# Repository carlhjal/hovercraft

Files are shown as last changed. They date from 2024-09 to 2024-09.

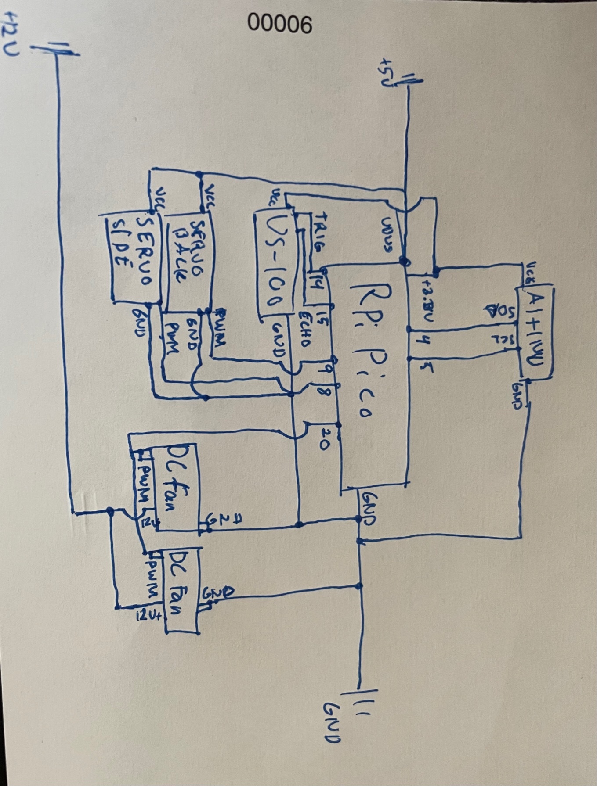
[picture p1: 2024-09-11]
diagram.jpg

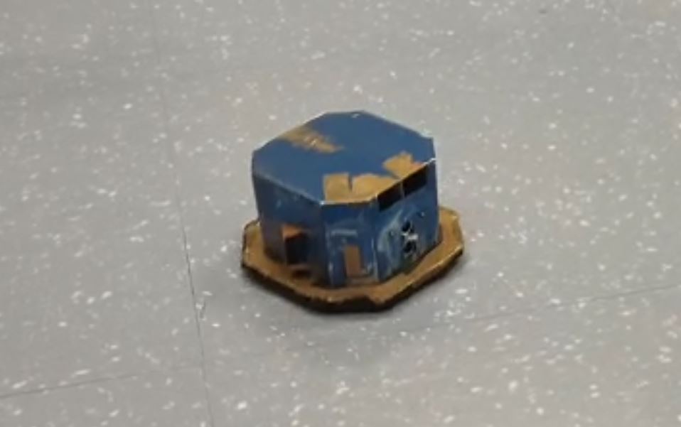
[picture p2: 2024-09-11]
image.JPG

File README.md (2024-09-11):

# Hovercraft

This is a Raspberry Pi Pico based project: a hovercraft capable of moving, steering and obstacle avoidance by use of an ultrasonic sensor and opening/closing shutters connected to its pressurized interior.

All the 3D printed parts from this project are available in the models folder.

PlatformIO is needed to build project "Robot Control Program".

A detailed/exploded view of the complete assembly is in the works..

Made as part of the Robotics Engineering Project course at the University of Tartu.

## Bill of materials
- x1 Raspberry Pi Pico
- x1 Breadboard
- x2 Turnigy TG9 Servo
- x1 US-100 ultrasonic sensor
- x2 GFB0412EHS-DF00 DC Fan
- x1 YB1203000-USB Battery (12V and 5V power supply)
- x1 AltIMU-10 v5
- x2 3D printed rail parts - "rail_lower_servo_fitting.STL"
- x2 3D printed shutters with racks - "lower_rack.STL"
- x1 3D printed US-100 fitting - "us-100-fitting.STL"
- x1 3D printed opening to fan duct - "intake_duct_smaller_fans.STL"
- x2 3D printed gear - "gear_final.STL"
- x1 3D printed base extender - "extension_plate.STL"
- x1 bottom skirt from extra durable trashbag
- x15 Male-to-male jumper cables
- x8 Male-to-female jumper cables
- x4 10mm M3 bolts with reduced head size
- x2 10mm M3 bolts
- x6 M3 nuts
- x1 12v Breakout cable
- x1 5v USB breakout cable
- Brown packing tape for airleak sealing and securing parts
- x1 cut cardboard duct for directing airflow from side outlet
- x1 cut cardboard flap for offsetting steering bias
- x1 cut cardboard for securing IMU on bottom plate

Any .STL files are available under models/stl_files

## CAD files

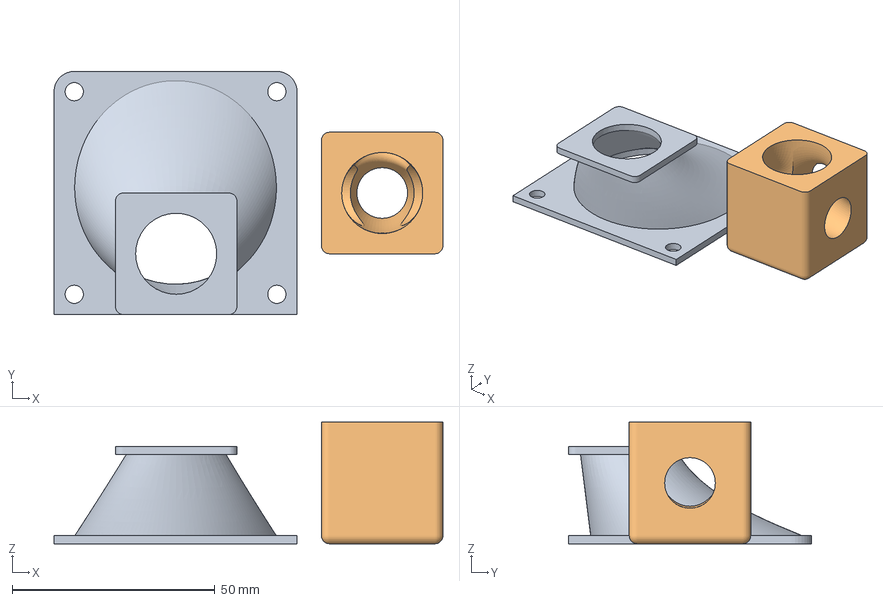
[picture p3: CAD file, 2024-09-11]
models/stl_files/air-divider^robotassembly.3mf
96.0 x 60.0 x 30.0 mm
duct-post-fan^robotassembly.STL
air-divider^robotassembly.STL

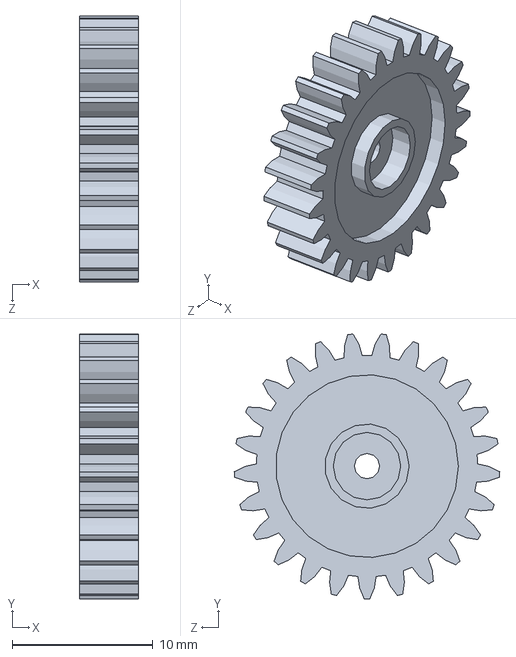
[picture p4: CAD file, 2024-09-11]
models/gear_final_asm.SLDPRT
4.20 x 18.8 x 18.9 mm

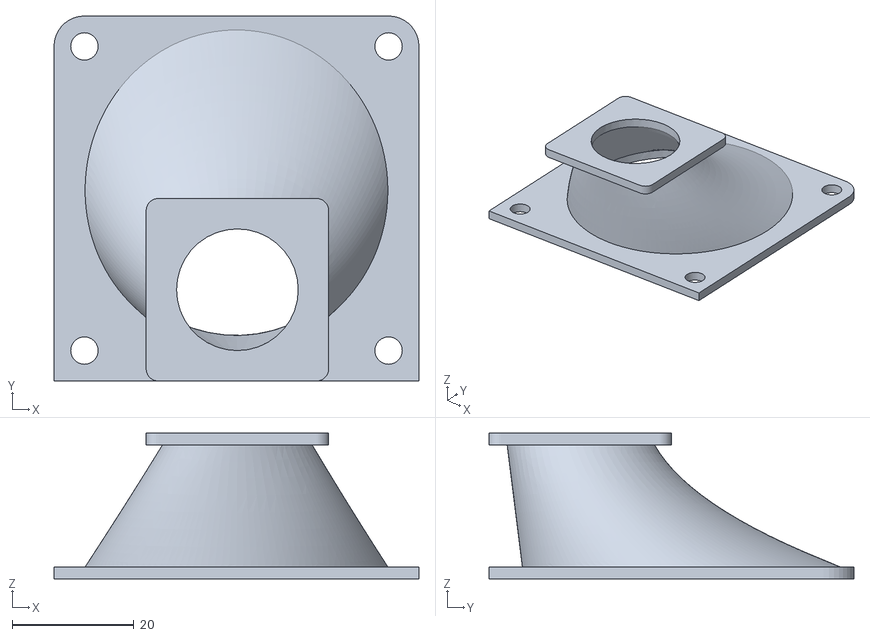
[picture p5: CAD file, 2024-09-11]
models/stl_files/duct-post-fan^robotassembly.STL
60.0 x 60.0 x 24.0

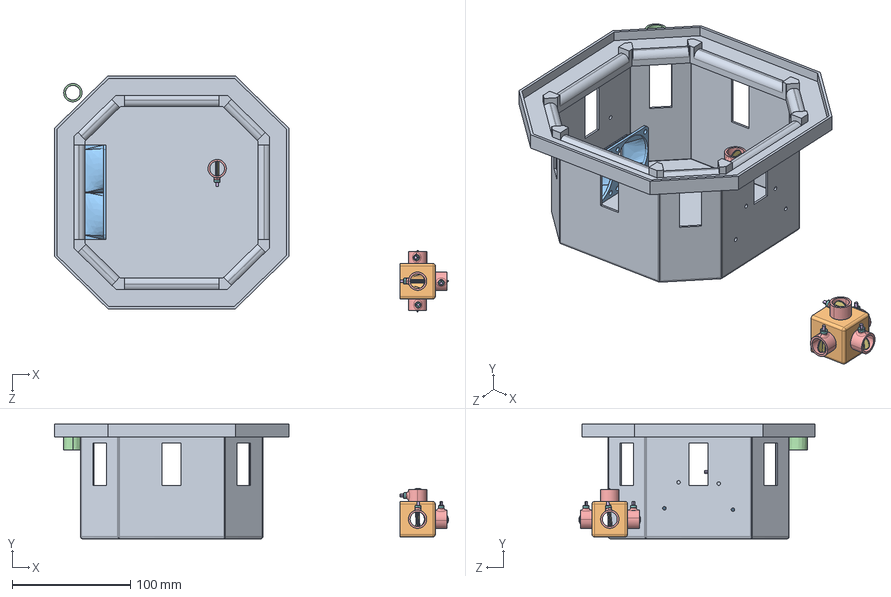
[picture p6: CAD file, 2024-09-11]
models/robotassembly.STEP
333.3 x 97.0 x 199.8 mm
air-divider^robotassembly
intake_duct_smaller_fans
tube_fitting
Butterfly_valve_tube x 5
shaft^Butterfly_valve x 5
plate^Butterfly_valve x 5
cap^Butterfly_valve x 5
extension_plate

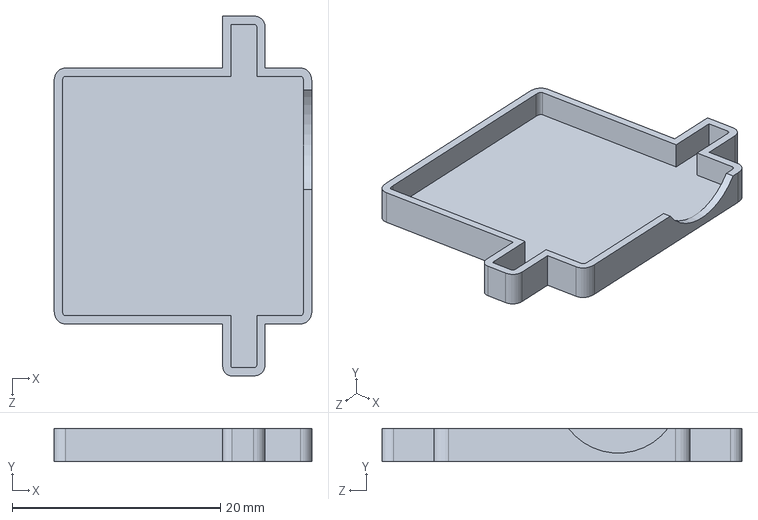
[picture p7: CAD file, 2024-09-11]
models/fitting_for_serv.SLDPRT
24.8 x 3.20 x 34.6 mm

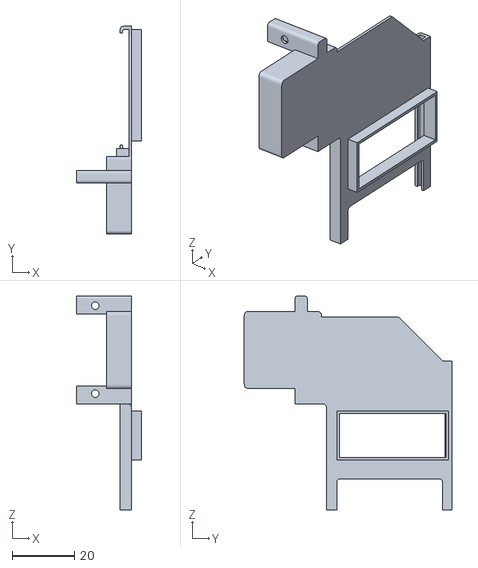
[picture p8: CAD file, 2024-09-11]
models/stl_files/rail_lower_servo_fitting.STL
20.8 x 66.5 x 68.6

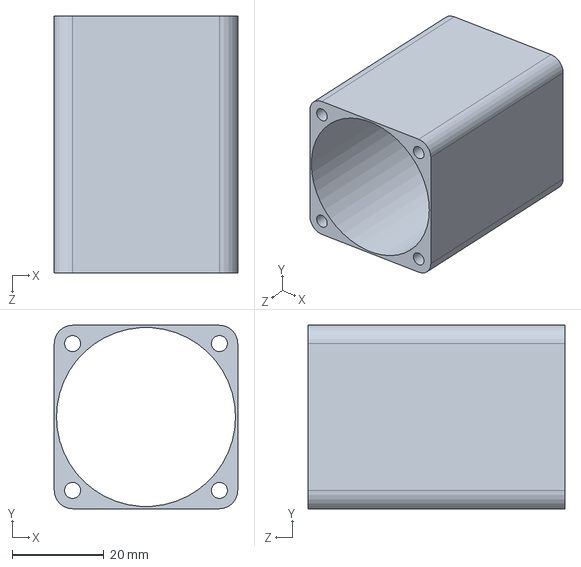
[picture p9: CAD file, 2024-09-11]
models/smaller_fan_rough.SLDPRT
40.0 x 40.0 x 56.0 mm

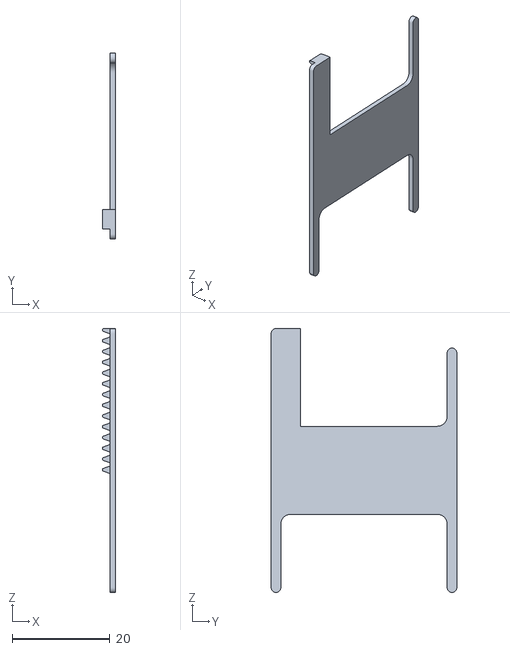
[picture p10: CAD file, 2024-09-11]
models/stl_files/lower_rack.STL
2.70 x 38.0 x 54.0

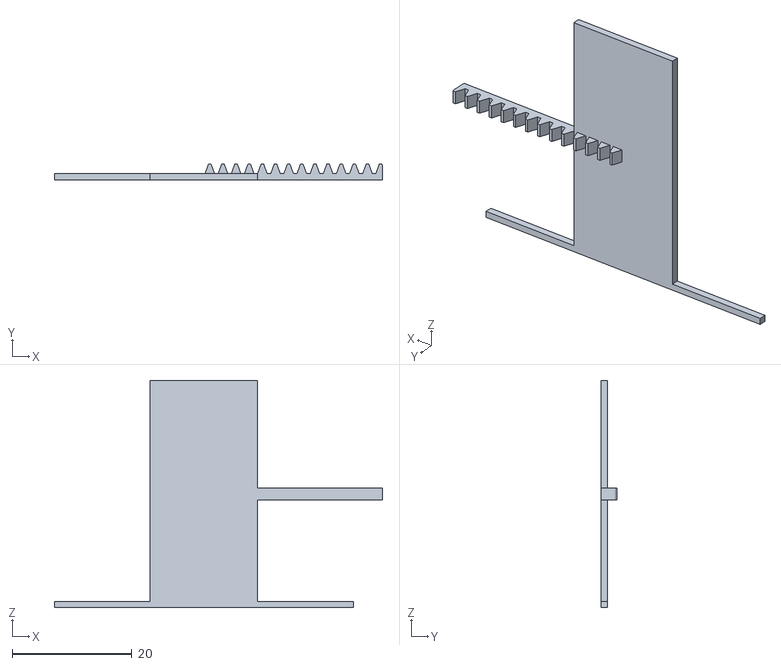
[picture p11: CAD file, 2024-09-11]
models/stl_files/other_rack.STL
54.9 x 2.70 x 38.0

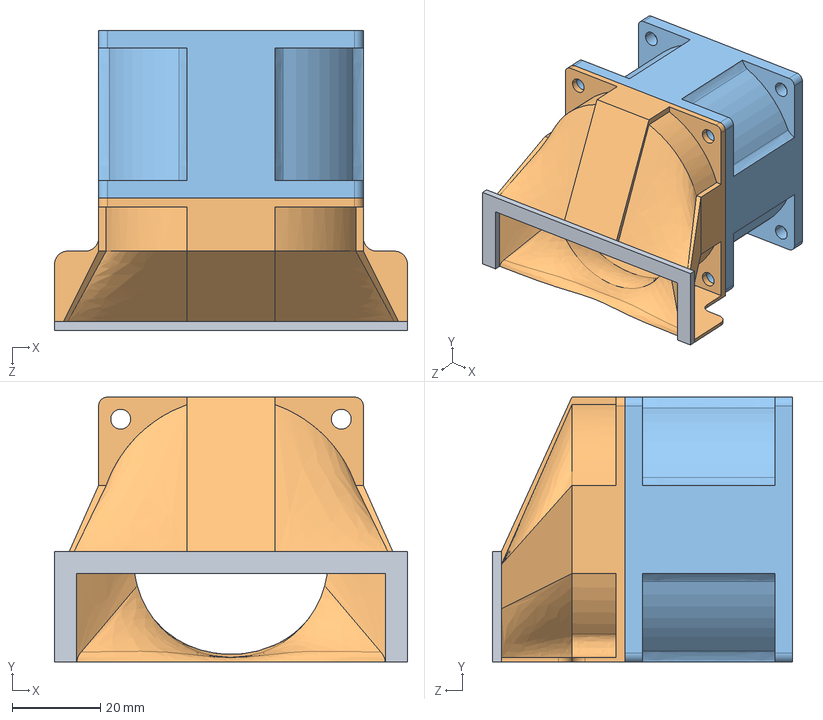
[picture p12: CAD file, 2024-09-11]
models/fan-intake.STEP
80.0 x 60.0 x 68.0 mm
Intake_duct_2.0
rough_fan

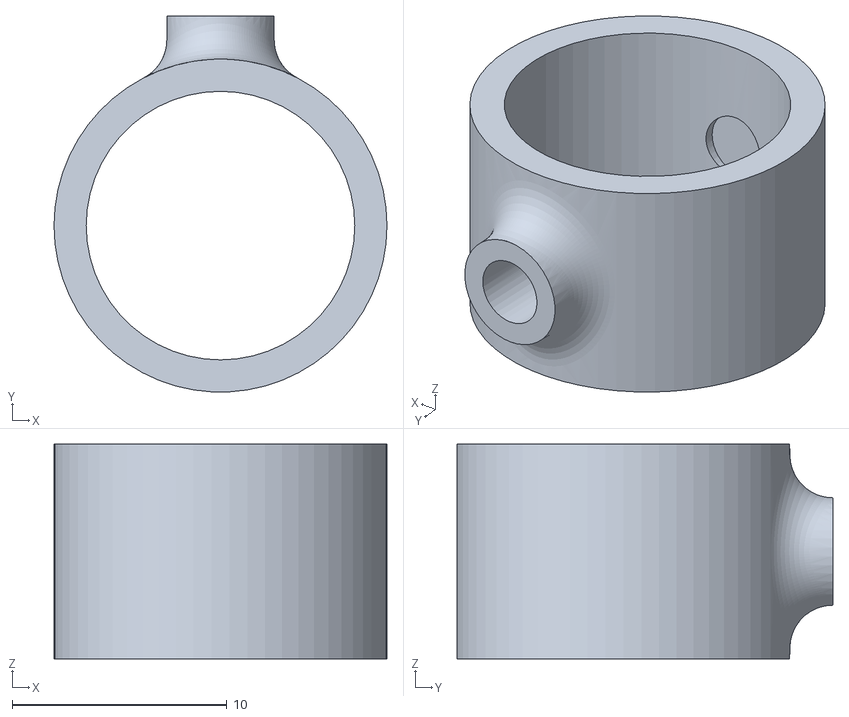
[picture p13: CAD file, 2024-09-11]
models/stl_files/Butterfly_valve - Butterfly_valve_tube-1-1.STL
15.5 x 17.5 x 10.00

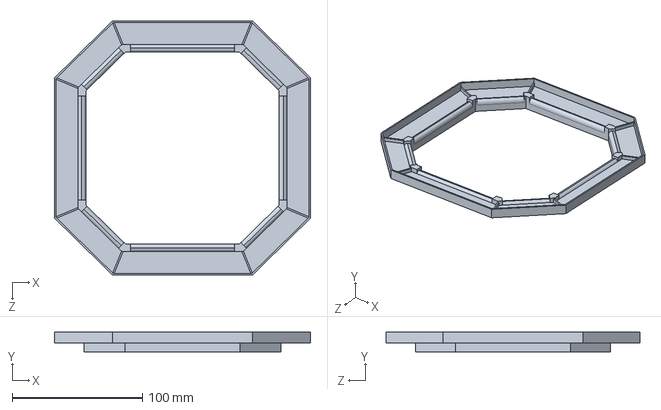
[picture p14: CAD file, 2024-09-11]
models/extension_plate.SLDPRT
196.3 x 15.0 x 195.0 mm

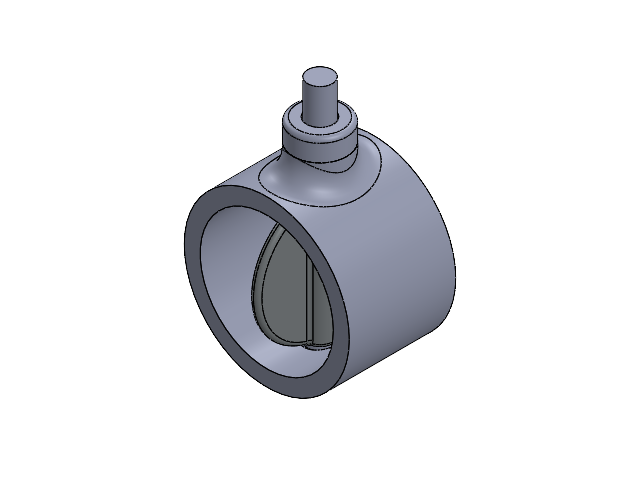
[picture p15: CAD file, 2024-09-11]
models/Butterfly_valve.SLDASM
Butterfly_valve_tube
shaft^Butterfly_valve
plate^Butterfly_valve
cap^Butterfly_valve

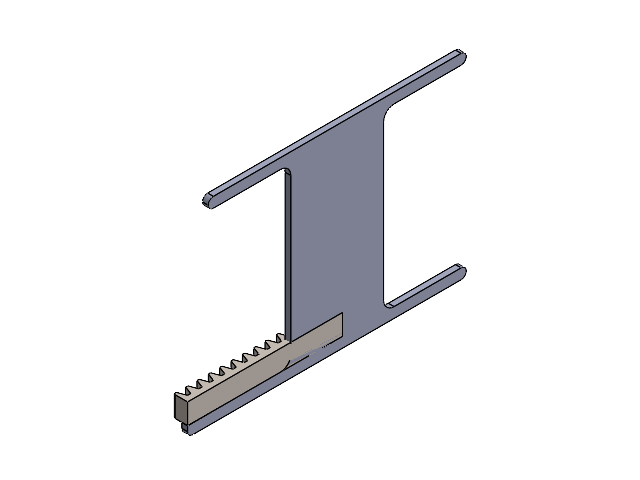
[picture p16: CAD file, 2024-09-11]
models/rail_and_shutter_test.SLDASM
Part4^Copy of other_rack_test_rail_and_shutter_test
rack spur rectangular_am

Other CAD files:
models/rail_and_shutter.SLDASM
models/other_rack_test.SLDASM
models/duct_to_lift.SLDPRT
models/stl_files/sturdy_rack_shutter.STL
models/Butterfly_valve_tube.SLDPRT
models/Intake_duct_2.0.SLDPRT
models/balloon_fitting.SLDPRT
models/duct_to_lift_direct.SLDPRT
models/fan-intake.SLDASM
models/gear.SLDPRT
models/gear_final.SLDPRT
models/gear_thinner.SLDPRT
models/intake_duct.SLDPRT
models/intake_duct_smaller_fans.SLDPRT
models/rack_final.SLDPRT
models/rack_final_version2.SLDPRT
models/rail.SLDPRT
models/robotassembly.SLDASM
models/robox.SLDPRT
models/rough_fan.SLDPRT
models/shell.SLDPRT
models/stl_files/Assem1 - Part2^Assem1-1.STL
models/stl_files/Assem1 - rack spur rectangular_am-1.STL
models/stl_files/Butterfly_valve - cap^Butterfly_valve-1-1.STL
models/stl_files/Butterfly_valve - plate^Butterfly_valve-1-1.STL
models/stl_files/Butterfly_valve - shaft^Butterfly_valve-1-1.STL
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

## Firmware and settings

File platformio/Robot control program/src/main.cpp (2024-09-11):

#include <Arduino.h>
#include <LIS3MDL.h>
#include <LSM6.h>
#include <Wire.h>
#include <MBED_RP2040_PWM.h>
#include <Servo.h>
#include <MBED_RPi_Pico_ISR_Timer.h>
#include <MBED_RPi_Pico_TimerInterrupt.h>
#include <SimpleKalmanFilter.h>
#include <math.h>
#include <function_declarations.h>

#define PWM_PIN 20
#define DIV_PIN 26
#define MEASUREMENT_INTERVAL_MS 40
#define TRIG_HIGH_TIME_US 10
#define TRIG_PIN 14
#define ECHO_PIN 15
#define BACK_SERVO_PIN 9
#define SIDE_SERVO_PIN 8
#define CLOSED 120
#define OPEN 0

#define USING_MBED_RPI_PICO_TIMER_INTERRUPT true
#define _TIMERINTERRUPT_LOGLEVEL_ 4

Servo back_servo;
Servo side_servo;
LIS3MDL mag;
LSM6 imu;
mbed::PwmOut* fan_pwm = NULL;
MBED_RPI_PICO_Timer timer_take_measurement(1);
MBED_RPI_PICO_Timer timer_trig_low(2);
SimpleKalmanFilter ultrasonic_kalman_filter(1,1,0.1);
SimpleKalmanFilter acc_kalman_filter(1000,1000,0.4);
SimpleKalmanFilter gyro_kalman_filter(1000,1000,0.2);

enum bot_state {
  IDLE_HOVER,
  FORWARD,
  TURBO_BOOST,
  ROTATE,
  GRACEFULLY_STOP,
  EMERGENCY_STOP,
  SLIDING
};

bot_state curr_state = IDLE_HOVER;

const float duty_cycle = 10.0f;
const float freq = 25000.0f;
const float hover_duty_cycle = 80.0f;
const float rotate_duty_cycle = 95.0f;
const float emergency_stop_duty_cycle = 40.0f;
const float gracefully_stop_duty_cycle = 50.0f;
const uint16_t rotate_time_ms = 2000;
const uint16_t turbo_boost_time_ms = 2000;
const uint16_t emergency_stop_timer_ms = 2000;
const uint16_t idle_hover_timer_ms = 2000;
const uint16_t graceful_stop_timer_ms = 2000;
const uint8_t safe_distance = 30;
const uint8_t safe_enough_distance = 35;
const uint8_t acc_dt = 50;
const float acc_dt_s = 0.05;
const int initial_cal_time = 10000;
const float decay = 1.5;
const int imu_timer = 100;

float turbo_boost_duty_cycle = 100.0f;
float forward_duty_cycle = 85.0f;
long back_servo_val = 120;
long side_servo_val = 120;
float dist;
float v_estimate;
float imu_acc_read;
float last_imu_acc_est;
float imu_acc_est;
float filtered_dist = 0;
bool flag_rotate = false;
unsigned long rotate_timer;
unsigned long turbo_boost_timer;
unsigned long emergency_stop_timer;
unsigned long idle_hover_timer;
unsigned long idle_hover_calibration_timer;
unsigned long graceful_stop_timer;
unsigned long acc_dt_timer;
unsigned long cal_timer;
float inaccuracy = 0;

volatile uint16_t ultrasonic_read;
volatile long time_echo;
volatile long time_start;
volatile bool get_dist = false;

// if using default imu calibration values
LIS3MDL::vector<int16_t> m_min = {-32767, -32767, -32767};
LIS3MDL::vector<int16_t> m_max = {+32767, +32767, +32767};
// if calibrating
//LIS3MDL::vector<int16_t> m_min = {0, 0, 0};
//LIS3MDL::vector<int16_t> m_max = {0, 0, 0};


unsigned long imu_poll = 0;
float imu_read;
float v_avg = 0;

void setup() {
  setPWM(fan_pwm, PWM_PIN, freq, duty_cycle);
  back_servo.attach(BACK_SERVO_PIN);
  side_servo.attach(SIDE_SERVO_PIN);
  Serial.begin(9600);
  Wire.begin();
  delay(1000);
  if (!mag.init()) {
    Serial.println("Failed to initialize magnetometer");
    while(1);
  }
  if (!imu.init()) {
    Serial.println("Failed to initialize gyro and accelerometer");
    while(1);
  }
  Serial.println("hello");
  delay(1000);
  mag.enableDefault();
  imu.enableDefault();

  if (timer_take_measurement.attachInterruptInterval(MEASUREMENT_INTERVAL_MS*1000, timer_start_m_handler)) {
    //worked
  }
  if (timer_trig_low.attachInterruptInterval(TRIG_HIGH_TIME_US, timer_trig_low_handler)) {
    timer_trig_low.disableTimer();
  }
  attachInterrupt(digitalPinToInterrupt(ECHO_PIN), echo_handler, FALLING);
  digitalWrite(TRIG_PIN, LOW);
  curr_state = IDLE_HOVER;
  delay(5000);
  cal_timer = millis()+initial_cal_time;
  initial_calibration();
} 

void loop() {
  if (get_dist) {
    dist = 0.6*dist + 0.4*calc_dist(time_echo);
    filtered_dist = ultrasonic_kalman_filter.updateEstimate(dist);
    get_dist = false;
  }

  switch (curr_state) {
    case IDLE_HOVER:
      hover_nicely();
      if (should_calibrate()) {
        accel_calibrate();
      }
      if (!hover_cooldown_over()) {
      } else if (should_rotate()) {
        engage_rotation_mode();
      } else if (should_turbo_boost()) {
        engage_turbo_drive();
      }
    break;

    case FORWARD: 
      creep_forward();
      if (millis() > acc_dt_timer) {
        update_v_est();
      }
      if (should_emergency_stop()) {
        engage_emergency_stop();
      } else if (should_gracefully_stop()) {
        engage_graceful_stop();
      } else if (too_fast()) {
        engage_sliding_mode();
      } else if (too_slow()) {

      }
    break;

    case TURBO_BOOST:
      boost_like_no_tomorrow();
      if (millis() > acc_dt_timer) {
        update_v_est();
      }
      if (should_emergency_stop()) {
        engage_emergency_stop();
      } else if (enough_turbo()) {
        curr_state = FORWARD;
      } else if (too_fast()) {
        engage_sliding_mode();
      }
    break;

    case ROTATE:
      rotate();
      if (finished_rotate()) {
        engage_graceful_stop();
      }
    break;

    case GRACEFULLY_STOP:
      come_to_a_graceful_stop();
      if (should_emergency_stop()) {
        engage_emergency_stop();
      } else if (should_hover()) {
        engage_hover_mode();
      } else if (stuck()) {
        engage_emergency_stop();
      }
    break;

    case EMERGENCY_STOP:
      stop_fast();
      if (should_hover_post_emergency()) {
        engage_hover_mode();
      }
    break;

    case SLIDING:
      slide();
      if (millis() > acc_dt_timer) {
        update_v_est();
      }
      if (should_emergency_stop()) {
        engage_emergency_stop();
      } else if (should_gracefully_stop()) {
        engage_graceful_stop();
      } else if (too_slow()) {
        curr_state = FORWARD;
      }
    break;
  }

  imu.read();
  imu_read = 0.8*imu_read + 0.2*(imu.g.z+470);
  float rot_est = gyro_kalman_filter.updateEstimate(imu_read);
  imu_acc_read = (0.9*imu_acc_read + 0.1*-(imu.a.y));
  imu_acc_est = acc_kalman_filter.updateEstimate(imu_acc_read);
  imu_acc_est -= inaccuracy;

  Serial.println(filtered_dist);
  delay(10);
}

bool stuck() {
  if (filtered_dist <= safe_enough_distance) {
    return true;
  }
  return false;
}

void initial_calibration() {
  while (millis() < cal_timer) {
    if (millis() > acc_dt_timer) { 
      imu.read();
      imu_acc_read = (0.8*imu_acc_read + 0.2*-(imu.a.y));
      imu_acc_est = acc_kalman_filter.updateEstimate(imu_acc_read);
      acc_dt_timer = millis() + acc_dt;
      //Serial.println(imu_acc_est);
    }
    if (abs(imu_acc_est - last_imu_acc_est) < 200) {
      inaccuracy = imu_acc_est;
    }
    last_imu_acc_est = imu_acc_est;
  }
}

void accel_calibrate() {
  if (millis() > acc_dt_timer) { 
    imu.read();
    imu_acc_read = (0.8*imu_acc_read + 0.2*-(imu.a.y));
    imu_acc_est = acc_kalman_filter.updateEstimate(imu_acc_read);
    acc_dt_timer = millis() + acc_dt;
    if (abs(imu_acc_est - last_imu_acc_est) < 200) {
      inaccuracy = imu_acc_est;
    }
    last_imu_acc_est = imu_acc_est;
  }
}

bool too_slow() {
  if (v_estimate < 15) {
    if (forward_duty_cycle < 85) forward_duty_cycle++;
    if (turbo_boost_duty_cycle < 100) turbo_boost_duty_cycle++;
    return true;
  }
  return false;
}

bool should_calibrate() {
  if (millis() > idle_hover_calibration_timer) {
    return true;
  }
  return false;
}

bool too_fast() {
  if (v_estimate >=15) {
    if (forward_duty_cycle >= 82) forward_duty_cycle--;
    if (turbo_boost_duty_cycle > 90) turbo_boost_duty_cycle--;
    return true;
  }
  return false;
}

// v_estimate is more like a movement average, not actual velocity, but should be used to prevent the robot from accelerating way too fast in the case when friction happens to be exceptionally low.
// which happens sometimes.. like when the battery is fully charged.
void update_v_est() {
  v_estimate = v_estimate + abs(imu_acc_est-last_imu_acc_est)*(acc_dt_s)/10;
  if (v_estimate > 0) {
    v_estimate -= decay;
  } else {
    v_estimate += decay;
  }
  last_imu_acc_est = imu_acc_est;
  acc_dt_timer = millis() + acc_dt;
  Serial.println(v_estimate);
}

// scrapped as magnetometer seems broken
void get_mag_data() {
  mag.read();
  int32_t temp[2] = {mag.m.x, mag.m.y};
  float heading = atan2(temp[1], temp[0]) * 180 / PI;
  float mag_dec = 9.93;
  heading += mag_dec;
  if (heading < 0) heading += 360;
  //Serial.println(heading);
}

void slide() {
  setPWM(fan_pwm, PWM_PIN, freq, hover_duty_cycle);
  back_servo.write(OPEN);
  side_servo.write(CLOSED);
}

void stop_fast() {
  setPWM(fan_pwm, PWM_PIN, freq, emergency_stop_duty_cycle);
  back_servo.write(CLOSED);
  side_servo.write(CLOSED);
}

void come_to_a_graceful_stop() {
  setPWM(fan_pwm, PWM_PIN, freq, gracefully_stop_duty_cycle);
  back_servo.write(CLOSED);
  side_servo.write(CLOSED);
}

void rotate() {
  setPWM(fan_pwm, PWM_PIN, freq, rotate_duty_cycle);
  back_servo.write(CLOSED);
  side_servo.write(OPEN);
}

void boost_like_no_tomorrow() {
  setPWM(fan_pwm, PWM_PIN, freq, turbo_boost_duty_cycle);
  back_servo.write(OPEN);
  side_servo.write(CLOSED);
}

void creep_forward() {
  setPWM(fan_pwm, PWM_PIN, freq, forward_duty_cycle);
  back_servo.write(OPEN);
  side_servo.write(CLOSED);
}

void engage_hover_mode() {
  idle_hover_timer = millis() + idle_hover_timer_ms;
  idle_hover_calibration_timer = millis() + idle_hover_timer_ms/4;
  curr_state = IDLE_HOVER;
}

void hover_nicely() {
  setPWM(fan_pwm, PWM_PIN, freq, hover_duty_cycle);
  back_servo.write(CLOSED);
  side_servo.write(CLOSED);
}

void engage_sliding_mode() {
  curr_state = SLIDING;
  last_imu_acc_est = 0;
}

void engage_graceful_stop() {
  graceful_stop_timer = millis() + graceful_stop_timer_ms;
  curr_state = GRACEFULLY_STOP;
}

void engage_emergency_stop() {
  emergency_stop_timer = millis() + emergency_stop_timer_ms;
  curr_state = EMERGENCY_STOP;
}

void engage_rotation_mode() {
  rotate_timer = millis() + rotate_time_ms;
  curr_state = ROTATE;
}

void engage_turbo_drive() {
  turbo_boost_timer = millis() + rotate_time_ms;
  v_estimate = 0;
  curr_state = TURBO_BOOST;
}

bool should_turbo_boost() {
  if ((filtered_dist >= safe_enough_distance)) {
    return true;
  }
  return false;
}

bool should_hover() {
  if (millis() > graceful_stop_timer) {
    return true;
  }
  return false;
}

bool hover_cooldown_over() {
  if (millis() > idle_hover_timer) {
    return true;
  }
  return false;
}

bool should_hover_post_emergency() {
  if (millis() > emergency_stop_timer) {
    return true;
  }
  return false;
}

bool enough_turbo() {
  if (millis() > turbo_boost_timer) {
    return true;
  }
  return false;
}

bool should_gracefully_stop() {
  if (filtered_dist < safe_enough_distance) {
    return true;
  }
  return false;
}

bool should_emergency_stop() {
  if (dist < safe_distance) {
    return true;
  }
  return false;
}

bool finished_rotate() {
  if (millis() > rotate_timer && dist > safe_distance) {
    return true;
  } 
  return false;
}

bool should_rotate() {
  if (dist < safe_distance) return true;
  return false;
}

void echo_handler() {
  time_echo = micros() - time_start;
  get_dist = true;
}

void timer_trig_low_handler(uint alarm_num) {
  TIMER_ISR_START(alarm_num);
  digitalWrite(TRIG_PIN, LOW);
  timer_trig_low.disableTimer();
  time_start = micros()+3000;
  TIMER_ISR_END(alarm_num);
}

void timer_start_m_handler(uint alarm_num) {
  TIMER_ISR_START(alarm_num);
  digitalWrite(TRIG_PIN, HIGH);
  timer_trig_low.enableTimer();
  TIMER_ISR_END(alarm_num);
}

void calibrate_mag() {
  unsigned long cal_time = millis() + 10000;
  while (millis() < cal_time) {
    mag.read();
    m_min.x = min(m_min.x, mag.m.x);
    m_min.y = min(m_min.y, mag.m.y);
    m_min.z = min(m_min.z, mag.m.z);
    m_max.x = max(m_max.x, mag.m.x);
    m_max.y = max(m_max.y, mag.m.y);
    m_max.z = max(m_max.z, mag.m.z);
    Serial.println(millis());
    Serial.println(cal_time);
    delay(50);
  }
}

long calc_dist(long fly_time) {
  return (long)((fly_time/2)/29.1);
}
